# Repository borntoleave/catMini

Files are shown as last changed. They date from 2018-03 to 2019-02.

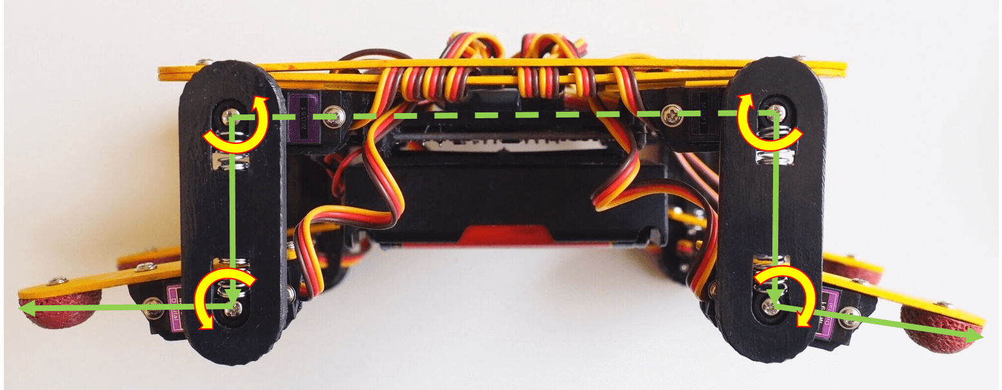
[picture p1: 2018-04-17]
Images/calibration.png

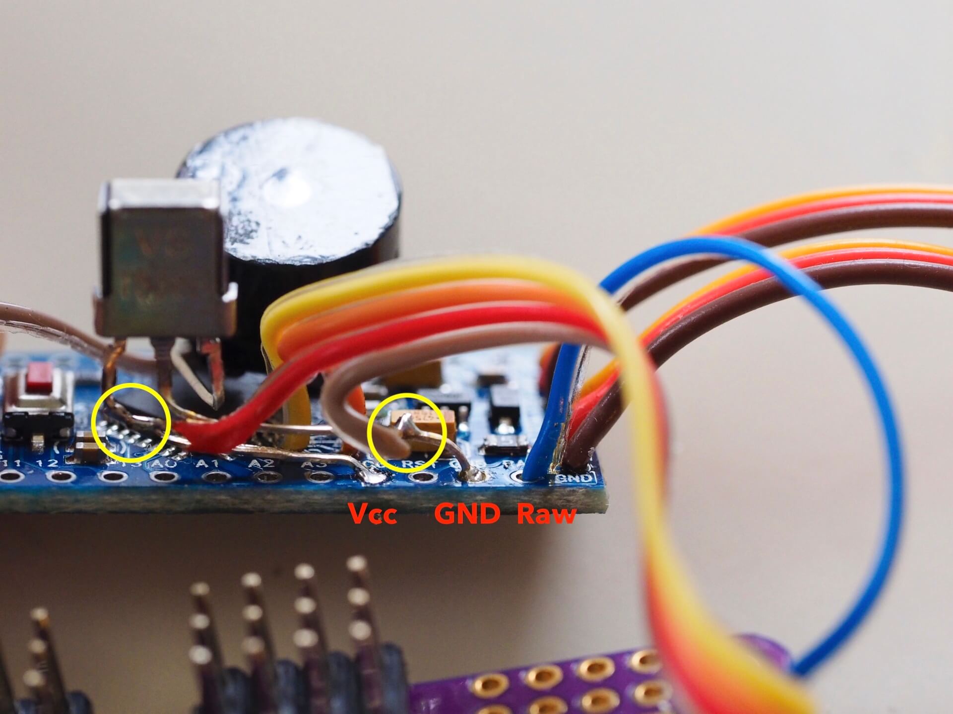
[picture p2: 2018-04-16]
Images/6.jpg

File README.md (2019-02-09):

# catMini
This is the course repository for catMini. Check out this demo video with my students racing them! https://youtu.be/T1OEnOONbIA

Structure
* Images/blockDiagram.png shows the circuit connection for catMini
* The test* folders with Arduino sketches are used for testing individual components' connections.
* writeConst folder contains the sketch to be uploaded to Arduino for storing calibration data
* catMini is the final sketch to be uploaded

This repo is obsolete since I've moved to my official repo for OpenCat: https://github.com/PetoiCamp/OpenCat
You can still find something interesting here.

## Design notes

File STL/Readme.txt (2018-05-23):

Recommanded Settings:
  material: ABS
  layer height: 0.1mm 
  infill: 100% 

Read the assmebling instructions in wiki thoroughly beforehand to understand how things are assembled. 

miniBody1 and miniBody2 shows the dimensions of the wooden frame. You can print them, but wooden ones are faster to make and has better strengh along the fiber direction. 

miniThigh holds the servo arm and allows it slide in the track. A spring pushes the servo arm in position. Check the assembling instructions for details.

miniToe is an old solution to increase friction. It should be printed with rubber-like soft material. 
I'm going to re-design a finger thimble like toe to replace it. 

Use M2 self-tapping screws to fix the frame and parts.

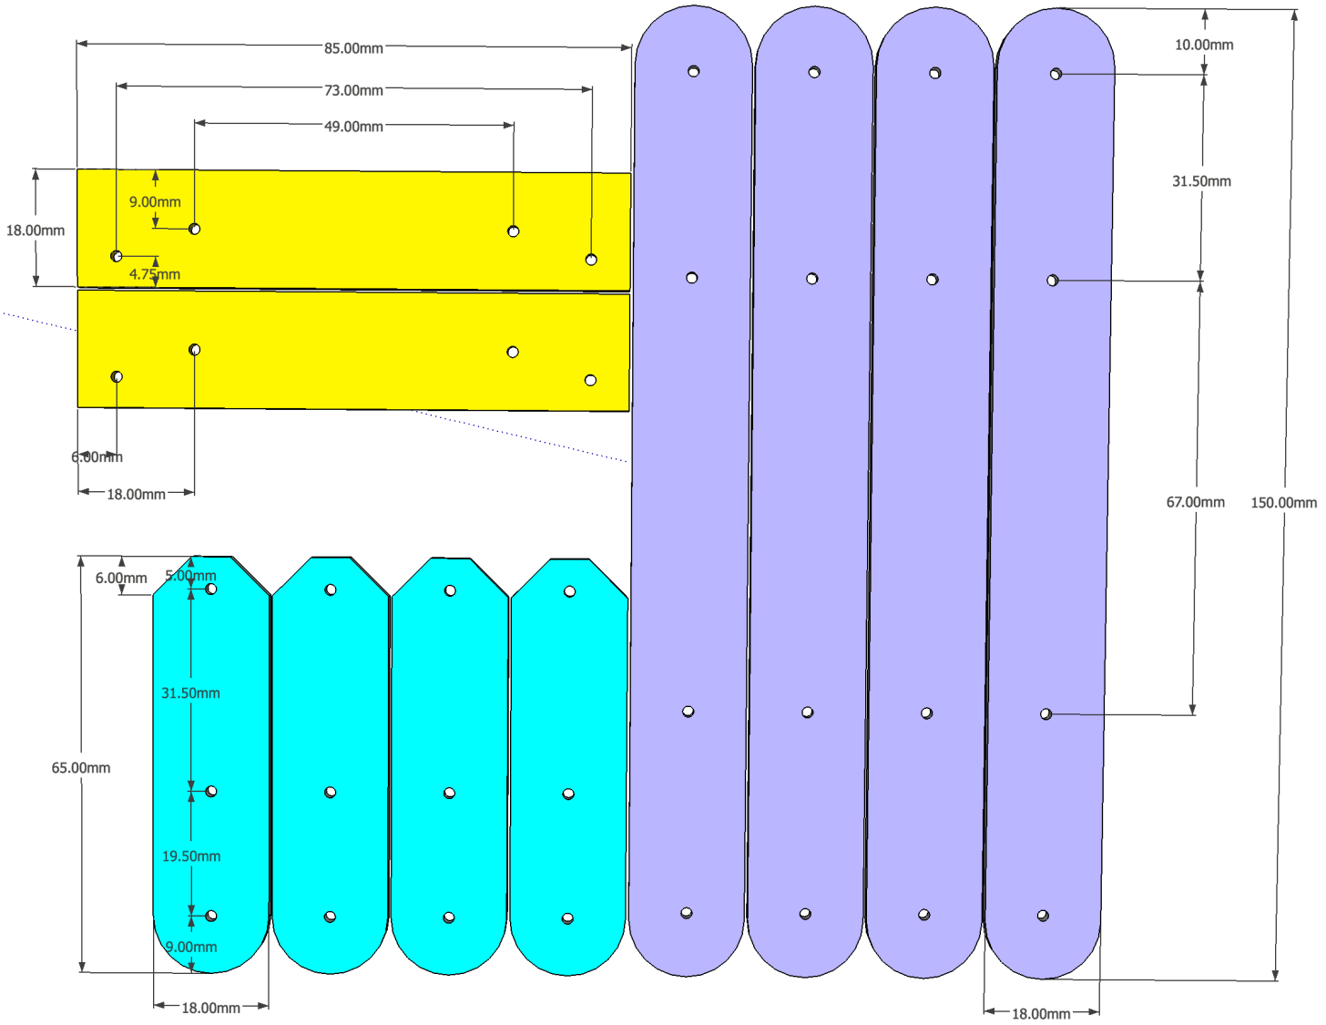
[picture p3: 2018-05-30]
Images/frameDim.png

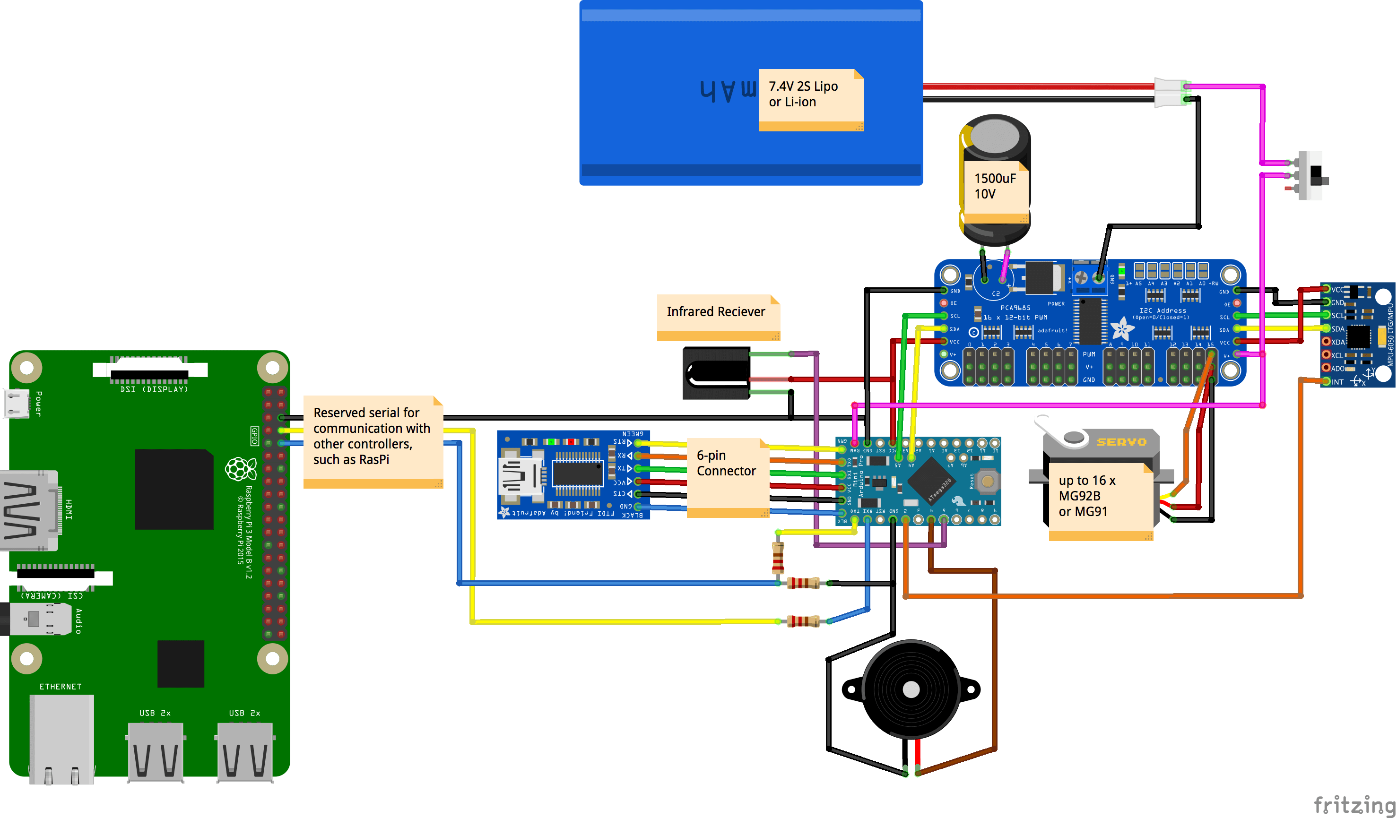
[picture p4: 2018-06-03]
Images/blockDiagram.png

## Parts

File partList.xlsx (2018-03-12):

Part List
 | Items | Quantity
Circuit | 18650/18500/14500 battery | 2
 | 2S battery holder | 1
 | slide switch | 1
 | MG91D/MG92B servos | 8
 | arduino pro mini 16Mhz 5V | 1
 | usb cable to mini usb | 1
 | FTDI | 1
 | MPU6050 | 1
 | PCA9685 servo driver | 1
 | IR remote kit | 1
 | 5V buzzer | 1
Frame | ABS filament | 1
 | spring | 8
 | Misc lab supply (wires, screws, box, etc)
 | 3D Printing and post processing (hrs) | 7

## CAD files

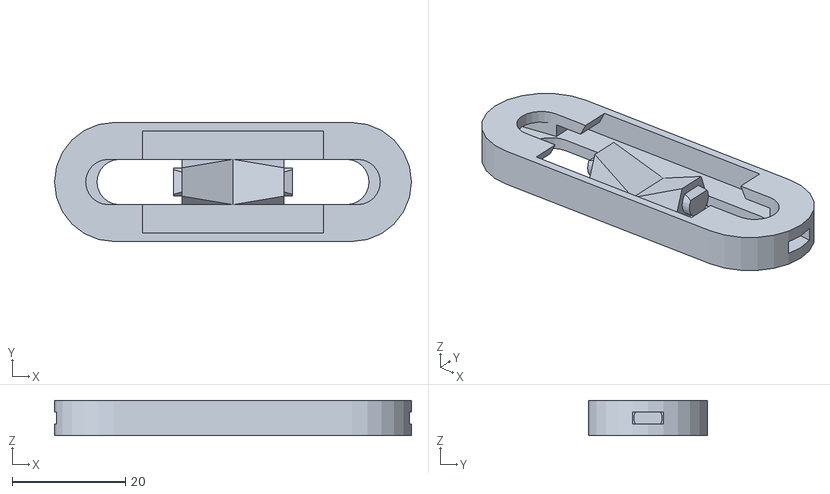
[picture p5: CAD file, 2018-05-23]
STL/1_miniThigh.stl
63.0 x 21.0 x 6.20

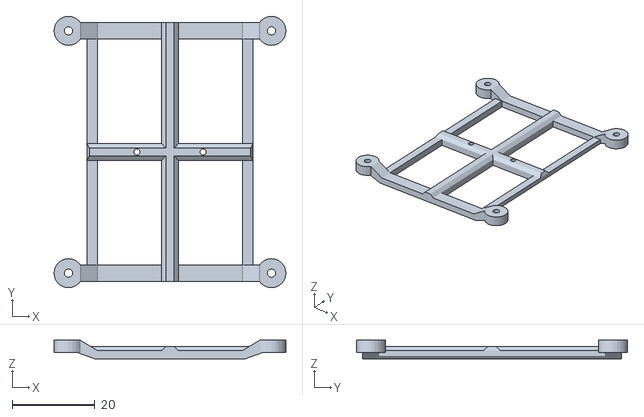
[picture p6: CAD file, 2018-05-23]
STL/mini_14500.stl
56.0 x 65.5 x 4.50

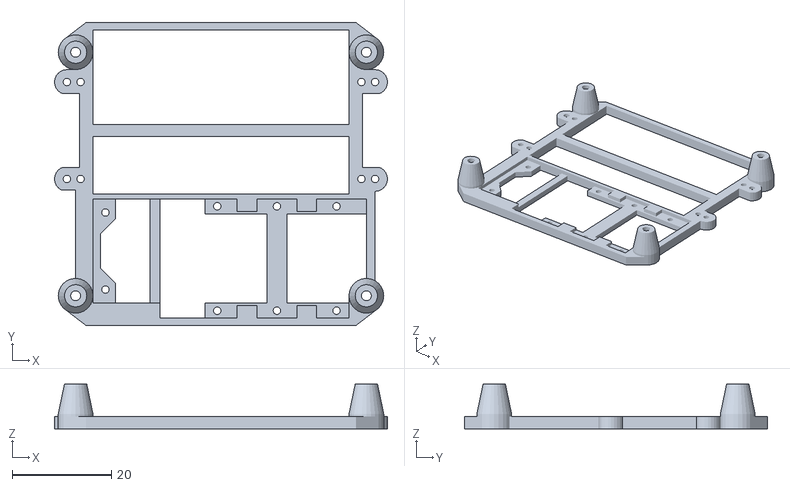
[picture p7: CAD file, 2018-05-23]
STL/miniCircuit.stl
67.0 x 61.0 x 9.00

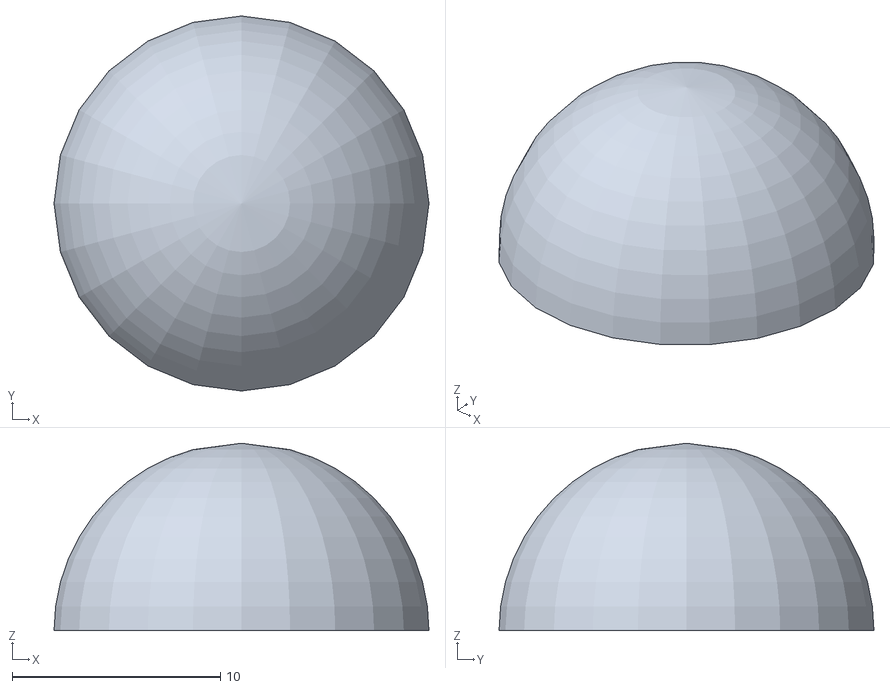
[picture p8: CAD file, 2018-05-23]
STL/1_miniToe_rubber.stl
18.0 x 18.0 x 9.00

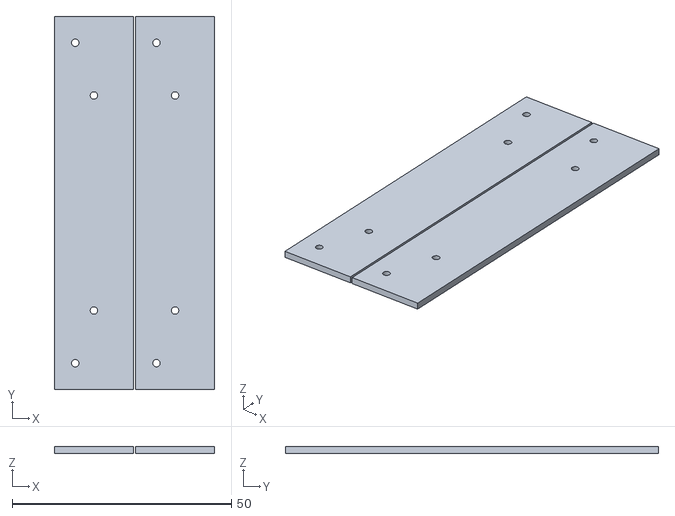
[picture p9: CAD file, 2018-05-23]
STL/all_miniBodyB.stl
36.5 x 85.0 x 1.50

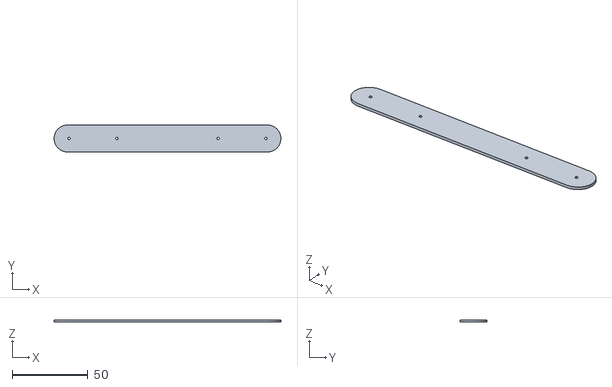
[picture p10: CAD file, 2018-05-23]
STL/1_miniBodyA.stl
150.0 x 18.0 x 1.50

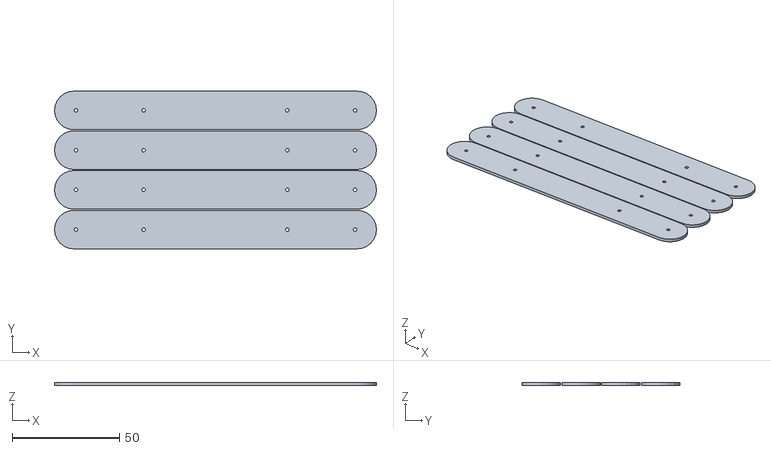
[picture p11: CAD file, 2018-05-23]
STL/all_miniBodyA.stl
150.0 x 73.5 x 1.50

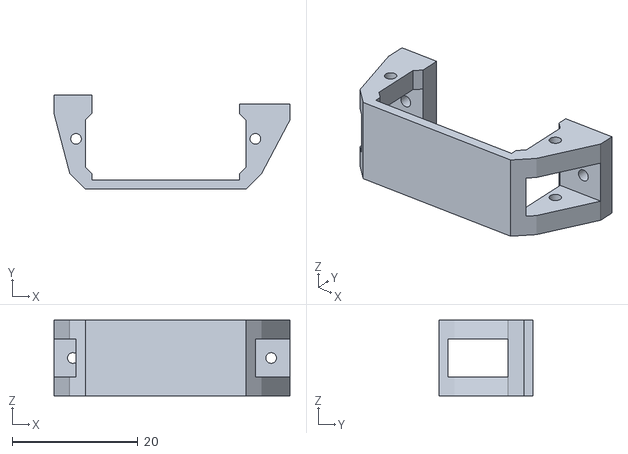
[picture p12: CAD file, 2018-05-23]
STL/1_miniServoHolder.stl
37.5 x 15.0 x 12.0

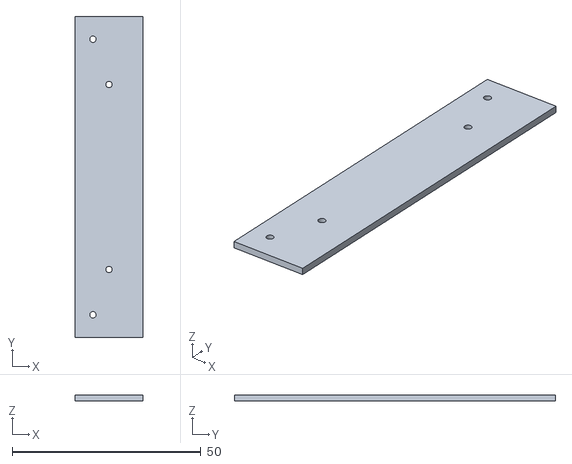
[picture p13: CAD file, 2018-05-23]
STL/1_miniBodyB.stl
18.0 x 85.0 x 1.50

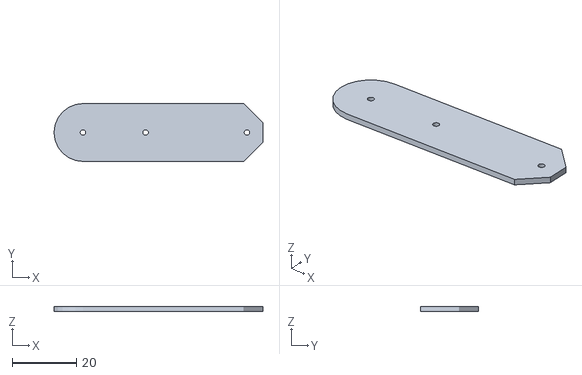
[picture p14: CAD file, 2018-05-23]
STL/1_miniShank.stl
65.0 x 18.0 x 1.50

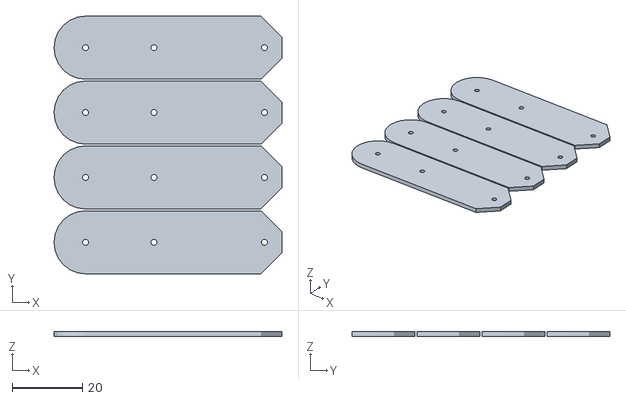
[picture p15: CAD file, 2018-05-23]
STL/all_miniShank.stl
65.0 x 73.5 x 1.50

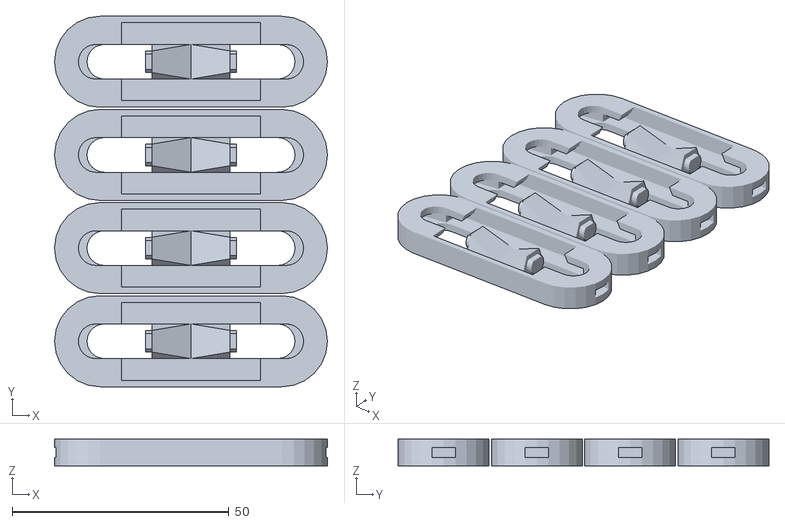
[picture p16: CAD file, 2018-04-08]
STL/all_miniThigh.stl
63.0 x 85.5 x 6.20

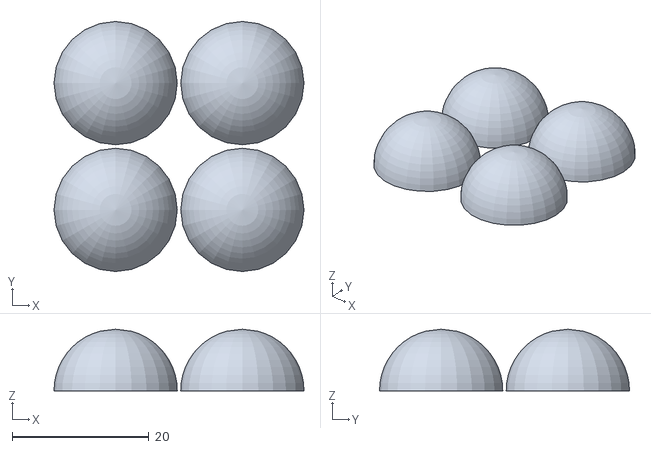
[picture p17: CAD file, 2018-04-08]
STL/all_miniToe_rubber.stl
36.5 x 36.5 x 9.00

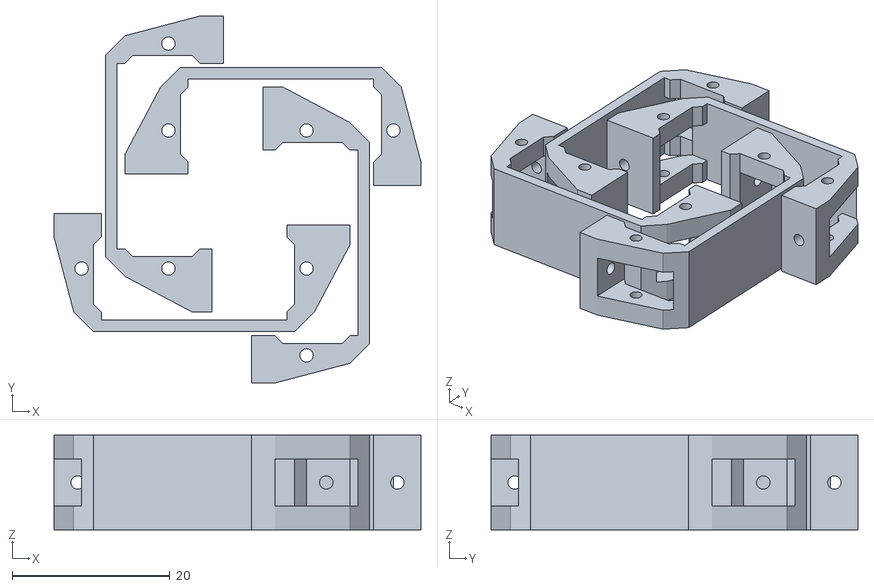
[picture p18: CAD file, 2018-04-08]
STL/all_miniServoHolder.stl
46.5 x 46.5 x 12.0

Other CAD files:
STL/mini_18650.stl

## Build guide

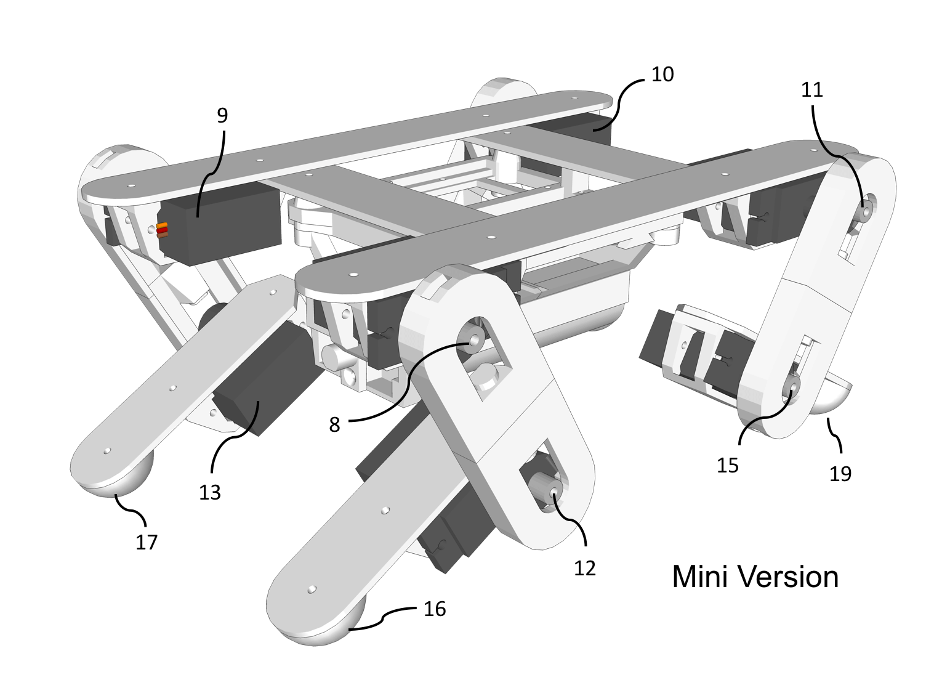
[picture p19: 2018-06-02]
Images/assembled.png

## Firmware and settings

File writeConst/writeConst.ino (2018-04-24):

/*
 *  Save calibration data and constants to EEPROM
 *  
 *  Copyright (c) 2018 Petoi LLC.  All right reserved.
 *  Written by Rongzhong Li
 *  
 *  This sketch also includes others' codes under MIT liscence. 
 *  See those liscences in corresponding sections.
 */

#define INIT true
#define LITE true
#include <EEPROM.h>
#define SPT(s) Serial.print(s)
#define SPTL(s) Serial.println(s)
#define SPTF(s) Serial.print(F(s))

#define MELODY 1023
#define PIN 0
#define CALIB 16
#define MIDSHIFT 32
#define ROTDIRECTION 48
#define RANGERATIO 64
#define MPUCALIB 80

#define DOF 16
#include <Wire.h>
#include <Adafruit_PWMServoDriver.h>

// called this way, it uses the default address 0x40
Adafruit_PWMServoDriver pwm = Adafruit_PWMServoDriver();
// you can also call it with a different address you want
//Adafruit_PWMServoDriver pwm = Adafruit_PWMServoDriver(0x41);

// Depending on your servo make, the pulse width min and max may vary, you
// want these to be as small/large as possible without hitting the hard stop
// for max range. You'll have to tweak them as necessary to match the servos you
// have!
#define SERVOMIN  150 // this is the 'minimum' pulse length count (out of 4096)
#define SERVOMAX  600 // this is the 'maximum' pulse length count (out of 4096)
#define BOUND 1/8
int range = SERVOMAX - SERVOMIN;
// our servo # counter

int8_t servoCalibs[DOF] = {};
char currentAng[DOF] = {};
int calibratedDuty0[DOF];
const char *gaits[] = {"vt", "rest", "calib", "balance",};
const char vt[] PROGMEM = { 30,
                            3, -3, -2,  2, 51, 45, 27, 22, -12,  3,  6, 22,
                            3, -2, -2,  2, 49, 45, 25, 22, -6,  3, 13, 22,
                            3, -2, -2,  1, 45, 45, 22, 22,  3,  3, 22, 22,
                            3, -1, -2,  1, 45, 45, 22, 22,  3,  3, 22, 22,
                            3, -1, -2,  1, 45, 45, 22, 22,  3,  3, 22, 22,
                            2,  1, -1,  1, 45, 46, 22, 22,  3,  1, 22, 20,
                            2,  1, -1, -1, 45, 49, 22, 25,  3, -6, 22, 13,
                            1,  2, -1, -1, 45, 51, 22, 27,  3, -12, 22,  6,
                            1,  2,  1, -1, 45, 54, 22, 29,  3, -19, 22,  1,
                            -1,  3,  1, -2, 45, 56, 22, 31,  3, -25, 22, -6,
                            -1,  3,  1, -2, 45, 59, 22, 33,  3, -33, 22, -12,
                            -2,  3,  1, -2, 45, 59, 22, 32,  3, -31, 22, -11,
                            -2,  3,  2, -2, 45, 56, 22, 31,  3, -25, 22, -6,
                            -3,  3,  2, -2, 45, 54, 22, 29,  3, -19, 22,  1,
                            -3,  3,  2, -2, 45, 51, 22, 27,  3, -12, 22,  6,
                            -3,  3,  2, -2, 45, 49, 22, 25,  3, -6, 22, 13,
                            -3,  3,  2, -2, 45, 45, 22, 22,  3,  3, 22, 22,
                            -2,  3,  2, -2, 45, 45, 22, 22,  3,  3, 22, 22,
                            -2,  3,  1, -2, 45, 45, 22, 22,  3,  3, 22, 22,
                            -1,  2,  1, -1, 45, 45, 22, 22,  3,  3, 22, 22,
                            -1,  2,  1, -1, 45, 45, 22, 22,  3,  3, 22, 22,
                            1,  1,  1, -1, 46, 45, 22, 22,  1,  3, 20, 22,
                            1,  1, -1,  1, 49, 45, 25, 22, -6,  3, 13, 22,
                            2, -1, -1,  1, 51, 45, 27, 22, -12,  3,  6, 22,
                            2, -1, -1,  1, 54, 45, 29, 22, -19,  3,  1, 22,
                            3, -2, -2,  1, 56, 45, 31, 22, -25,  3, -6, 22,
                            3, -2, -2,  2, 59, 45, 33, 22, -33,  3, -12, 22,
                            3, -3, -2,  2, 59, 45, 32, 22, -31,  3, -11, 22,
                            3, -3, -2,  2, 56, 45, 31, 22, -25,  3, -6, 22,
                            3, -3, -2,  2, 54, 45, 29, 22, -19,  3,  1, 22,
                            '\0'
                          };


const char rest[] PROGMEM = { 1,
                              1, 10,  1,  1, -3, -3,  3,  3, 60, 60, 60, 60, -30, -30, -30, -30, '\0'
                            };
const char calib[] PROGMEM = { 1,
                               1,  1,  1,  1,  1,  1,  1,  1,  1,  1,  1,  1,  1,  1,  1,  1, '\0'
                             };
const char balance[] PROGMEM = { 1,
                                 1, 20,  1,  1, -3, -3,  3,  3, 30, 30, 30, 30, 30, 30, 30, 30, '\0'
                               };
const char* const gaits_table[] PROGMEM = {vt, rest, calib, balance, };
char *dutyAng = new char [362];

void saveCalib(int8_t *var) {
  for (byte i = 0; i < DOF; i++) {
    EEPROM.update(CALIB + i, var[i]);
    calibratedDuty0[i] = SERVOMIN + range / 2 + float(middleShift(i) + var[i]) * range  * rotationDirection(i) / rangeRatio(i);
  }
}

void saveMPUcalib(int * var) {
  for (byte i = 0; i < 6; i++)
    EEPROM.update(MPUCALIB + i, var[i]);
}

void calibratedPWM(byte i, char dt) {
  currentAng[i] = dt;
  int duty = calibratedDuty0[i] + float(dt) * range  * rotationDirection(i) / rangeRatio(i);
  duty = min(SERVOMAX - range / 2 * BOUND, duty);
  duty = max(SERVOMIN + range / 2 * BOUND, duty);
  pwm.setPWM(pin(i), 0, duty);
}
void allCalibratedPWM(char * dutyAng) {
  for (byte i = 0; i < DOF; i++) {
    calibratedPWM(i, dutyAng[i]);
  }
}

void transform(char * current, char * target, byte offset = 0, float speedRatio = 1) {
  int *diff = new int[DOF - offset], maxDiff = 0;
  for (byte i = offset; i < DOF; i++) {
    diff[i - offset] =   current[i] - target[i - offset];
    maxDiff = max(maxDiff, abs( diff[i - offset]));
  }
  int steps = int(round(maxDiff / 3.0/*degreeStep*/ / speedRatio));
  for (byte s = 0; s < steps; s++)
    for (byte i = offset; i < DOF; i++) {
      int duty = (target[i] + (1 + cos(M_PI * s / steps)) / 2 * diff[i - offset]);
      calibratedPWM(i,  duty);
    }
  delete [] diff;
}

void shutServos() {
  delay(1000);
  for (byte i = 0; i < DOF; i++) {
    pwm.setPWM(i, 0, 4096);
  }
}

int8_t idxOfGait(const char * gait) {
  for (byte i = 0; i < sizeof(gaits) / sizeof(char*); i++)
    if (!strcmp(gaits[i], gait))
      return i;
  return -1;
}

int pgmCpy(char * dutyAng, const char * gait) {
  dutyAng--;
  strcpy_P(dutyAng, (char*)pgm_read_word(&(gaits_table[idxOfGait(gait)])));
  int period = dutyAng[0];
  dutyAng++;
  return period;
}

#include <EEPROM.h> //Needed to access the eeprom read write functions

byte pin(byte idx) {
  return (byte)EEPROM.read(PIN + idx);
}

int8_t middleShift(byte idx) {
  return (int8_t)EEPROM.read( MIDSHIFT + idx);
}
byte rangeRatio(byte idx) {
  return (byte)EEPROM.read(RANGERATIO + idx);
}
int8_t rotationDirection(byte idx) {
  return (int8_t)EEPROM.read(ROTDIRECTION + idx);
}
int8_t servoCalib(byte idx) {
  return (int8_t)EEPROM.read( CALIB + idx);
}

//This function will write a 2 byte integer to the eeprom at the specified address and address + 1
void EEPROMWriteInt(int p_address, int p_value)
{
  byte lowByte = ((p_value >> 0) & 0xFF);
  byte highByte = ((p_value >> 8) & 0xFF);

  EEPROM.update(p_address, lowByte);
  EEPROM.update(p_address + 1, highByte);
}

//This function will read a 2 byte integer from the eeprom at the specified address and address + 1
int EEPROMReadInt(int p_address)
{
  byte lowByte = EEPROM.read(p_address);
  byte highByte = EEPROM.read(p_address + 1);

  return ((lowByte << 0) & 0xFF) + ((highByte << 8) & 0xFF00);
}

void writeConst(bool lite = true) {
  // tone: pause,1,  2,  3,  4,  5,  6,  7,  1,  2, 3,
  // code: 0,    1,  3,  5,  6,  8,  10, 12, 13, 15, 17
  byte melody[] = {8, 13, 10, 13, 8,  0,  5,  8,  3,  5, 8,
                   8, 8,  32, 32, 8, 32, 32, 32, 32, 32, 8,
                  };
  EEPROM.update(MELODY, sizeof(melody));
  for (byte i = 0; i < sizeof(melody); i++)
    EEPROM.update(MELODY - 1 - i, melody[i]);

  int8_t calibs[] = {0,  0,  0,  0,  0,  0,  0,  0,  0,  0,  0,  0,  0,  0,  0,  0};

  int8_t middleShifts[] = {0, 45, 0, 0,
                           -45, -45, -45, -45,
                           0, 0, 0, 0,
                           0, 0, 0, 0
                          };
  int8_t rotationDirections[] = {1, -1, 1, 1,
                                 1, -1, 1, -1,
                                 1, -1, 1, -1,
                                 -1, 1, -1, 1
                                };
  byte mg90s = 180 , mg92b =  180;
  byte rangeRatios[] =  {mg92b, mg90s, mg92b, mg92b,
                         mg92b, mg92b, mg92b, mg92b,
                         mg92b, mg92b, mg92b, mg92b,
                         mg92b, mg92b, mg92b, mg92b
                        };

  for (byte i = 0; i < DOF; i++) {
    if (lite) {
      byte pins[] = {0, 0, 0, 0, 0, 0, 0, 0, 5, 4, 10, 11, 7, 6,8, 9};
      //byte pins[] = { 0, 1, 0, 0,  0, 0,  0, 0, 3, 2,  6, 7,  5, 4,  8, 9};
      EEPROM.update(PIN + i, pins[i]);
    }
    else {
      byte pins[] = { 1, 0, 15, 14,  3, 2,  8, 9, 5, 4,  10, 11,  7, 6,  12, 13};
      EEPROM.update(PIN + i, pins[i]);
    }
    if (INIT)
      EEPROM.update(CALIB + i, calibs[i]);
    EEPROM.update(MIDSHIFT + i, middleShifts[i]);
    EEPROM.update(ROTDIRECTION + i, rotationDirections[i]);
    EEPROM.update(RANGERATIO + i, rangeRatios[i]);
    SPT(servoCalib(i));
    SPT(',');
  }
  SPT('\n');
}

#define BUZZER 4
#define MELODY 1023
void beep(byte note, float duration = 10, int pause = 0, byte repeat = 1 ) {
  if (note == 0) {
    analogWrite(BUZZER, 0);
    delay(duration);
    return;
  }
  int freq = 220 * pow(1.059463, note);
  float period = 1000000.0 / freq / 2.0;
  for (byte r = 0; r < repeat; r++) {
    for (float t = 0; t < duration * 1000; t += period * 2) {
      analogWrite(BUZZER, 150);      // Almost any value can be used except 0 and 255
      // experiment to get the best tone
      delayMicroseconds(period);          // wait for a delayms ms
      analogWrite(BUZZER, 0);       // 0 turns it off
      delayMicroseconds(period);          // wait for a delayms ms
    }
    delay(pause);
  }
}

// http://wired.chillibasket.com/2015/01/calibrating-mpu6050/

// Arduino sketch that returns calibration offsets for MPU6050
//   Version 1.1  (31th January 2014)
// Done by Luis Ródenas <luisrodenaslorda@gmail.com>
// Based on the I2Cdev library and previous work by Jeff Rowberg <jeff@rowberg.net>
// Updates (of the library) should (hopefully) always be available at https://github.com/jrowberg/i2cdevlib

// These offsets were meant to calibrate MPU6050's internal DMP, but can be also useful for reading sensors.
// The effect of temperature has not been taken into account so I can't promise that it will work if you
// calibrate indoors and then use it outdoors. Best is to calibrate and use at the same room temperature.

/* ==========  LICENSE  ==================================
  I2Cdev device library code is placed under the MIT license
  Copyright (c) 2011 Jeff Rowberg

  Permission is hereby granted, free of charge, to any person obtaining a copy
  of this software and associated documentation files (the "Software"), to deal
  in the Software without restriction, including without limitation the rights
  to use, copy, modify, merge, publish, distribute, sublicense, and/or sell
  copies of the Software, and to permit persons to whom the Software is
  furnished to do so, subject to the following conditions:

  The above copyright notice and this permission notice shall be included in
  all copies or substantial portions of the Software.

  THE SOFTWARE IS PROVIDED "AS IS", WITHOUT WARRANTY OF ANY KIND, EXPRESS OR
  IMPLIED, INCLUDING BUT NOT LIMITED TO THE WARRANTIES OF MERCHANTABILITY,
  FITNESS FOR A PARTICULAR PURPOSE AND NONINFRINGEMENT. IN NO EVENT SHALL THE
  AUTHORS OR COPYRIGHT HOLDERS BE LIABLE FOR ANY CLAIM, DAMAGES OR OTHER
  LIABILITY, WHETHER IN AN ACTION OF CONTRACT, TORT OR OTHERWISE, ARISING FROM,
  OUT OF OR IN CONNECTION WITH THE SOFTWARE OR THE USE OR OTHER DEALINGS IN
  THE SOFTWARE.
  =========================================================
*/

// I2Cdev and MPU6050 must be installed as libraries
#include "I2Cdev.h"
#include "MPU6050.h"
#include "Wire.h"

///////////////////////////////////   CONFIGURATION   /////////////////////////////
//Change this 3 variables if you want to fine tune the skecth to your needs.
int discard = 100;
int buffersize = 1000;   //Amount of readings used to average, make it higher to get more precision but sketch will be slower  (default:1000)
int acel_deadzone = 8;   //Acelerometer error allowed, make it lower to get more precision, but sketch may not converge  (default:8)
int giro_deadzone = 1;   //Giro error allowed, make it lower to get more precision, but sketch may not converge  (default:1)

// default I2C address is 0x68
// specific I2C addresses may be passed as a parameter here
// AD0 low = 0x68 (default for InvenSense evaluation board)
// AD0 high = 0x69
//MPU6050 mpu;
MPU6050 mpu(0x68); // <-- use for AD0 high

int16_t ax, ay, az, gx, gy, gz;

int mean_ax, mean_ay, mean_az, mean_gx, mean_gy, mean_gz, state = 0;
int ax_offset, ay_offset, az_offset, gx_offset, gy_offset, gz_offset;

int t = 0;
int tPeriod = 1;
byte offset;
char token;
#define CMD_LEN 10
char lastCmd[CMD_LEN] = {};
bool printMPU = false;
int mpuOffset[6];
void setup() {
  // join I2C bus (I2Cdev library doesn't do this automatically)
#if I2CDEV_IMPLEMENTATION == I2CDEV_ARDUINO_WIRE
  Wire.begin();
  TWBR = 24; // 400kHz I2C clock (200kHz if CPU is 8MHz)
#elif I2CDEV_IMPLEMENTATION == I2CDEV_BUILTIN_FASTWIRE
  Fastwire::setup(400, true);
#endif

  Serial.begin(57600);
  Serial.setTimeout(5);
  while (!Serial);

  for (byte i = 0; i < 6; i++)
    SPTL(EEPROMReadInt(MPUCALIB + i * 2));
  // initialize device
  mpu.initialize();

  // wait for ready
  while (Serial.available() && Serial.read()); // empty buffer
  /*while (!Serial.available()){
    Serial.println(F("Send any character to start sketch.\n"));
    delay(1500);
    }
    while (Serial.available() && Serial.read()); // empty buffer again
  */
  SPT(F("* RoPet Writing Constants to EEPROM *\n"));
  writeConst(LITE); // only run for the first time when writing to the board.

  // servo
  { pwm.begin();
    pwm.setPWMFreq(60);  // Analog servos run at ~60 Hz updates
    delay(200);

    strcpy(lastCmd, "rest");
    pgmCpy(dutyAng, "rest");
    for (byte i = 0; i < DOF; i++) {
      servoCalibs[i] = servoCalib(i);
      calibratedDuty0[i] =  SERVOMIN + range / 2 + float(middleShift(i) + servoCalibs[i]) * range   * rotationDirection(i) / rangeRatio(i);
      calibratedPWM(i, dutyAng[i]);
    }
    shutServos();
    token = 'd';
  }
  beep(30);

  // start message
  Serial.println("\nMPU6050 Calibration Sketch");
  delay(2000);
  Serial.println("\nYour MPU6050 should be placed in horizontal position, with package letters facing up. \nDon't touch it until you see a finish message.\n");
  delay(3000);
  // verify connection
  Serial.println(mpu.testConnection() ? "MPU6050 connection successful" : "MPU6050 connection failed");
  delay(1000);
  // reset offsets
  mpu.setXAccelOffset(0);
  mpu.setYAccelOffset(0);
  mpu.setZAccelOffset(0);
  mpu.setXGyroOffset(0);
  mpu.setYGyroOffset(0);
  mpu.setZGyroOffset(0);
}

void loop() {
  if (state == 0) {
    Serial.println("\nReading sensors for first time...");
    meansensors();
    state++;
    delay(1000);
  }

  if (state == 1) {
    Serial.println("\nCalculating offsets...");
    calibration();
    state++;
    delay(1000);
  }

  if (state == 2) {
    meansensors();
    Serial.println("\nFINISHED!");
    Serial.print("\nSensor readings with offsets:\t");
    Serial.print(mean_ax);
    Serial.print("\t");
    Serial.print(mean_ay);
    Serial.print("\t");
    Serial.print(mean_az);
    Serial.print("\t");
    Serial.print(mean_gx);
    Serial.print("\t");
    Serial.print(mean_gy);
    Serial.print("\t");
    Serial.println(mean_gz);
    Serial.print("Your offsets:\t");
    Serial.print(ax_offset);
    Serial.print("\t");
    Serial.print(ay_offset);
    Serial.print("\t");
    Serial.print(az_offset);
    Serial.print("\t");
    Serial.print(gx_offset);
    Serial.print("\t");
    Serial.print(gy_offset);
    Serial.print("\t");
    Serial.println(gz_offset);
    Serial.println("\nData is printed as: acelX acelY acelZ giroX giroY giroZ");
    Serial.println("Check that your sensor readings are close to 0 0 16384 0 0 0");
    Serial.println("If calibration was succesful write down your offsets so you can set them in your projects using something similar to mpu.setXAccelOffset(youroffset)");

    mpuOffset[0] = ax_offset;
    mpuOffset[1] = ay_offset;
    mpuOffset[2] = az_offset;
    mpuOffset[3] = gx_offset;
    mpuOffset[4] = gy_offset;
    mpuOffset[5] = gz_offset;

    for (byte i = 0; i < 6; i++)
      EEPROMWriteInt(MPUCALIB + i * 2, mpuOffset[i]);

    mpu.setXAccelOffset(ax_offset);
    mpu.setYAccelOffset(ay_offset);
    mpu.setZAccelOffset(az_offset);
    mpu.setXGyroOffset(gx_offset);
    mpu.setYGyroOffset(gy_offset);
    mpu.setZGyroOffset(gz_offset);
    //while (1);
    state = 3;
  }

  char cmd[CMD_LEN] = {};
  byte newCmd = 0;
  if (t == 0 && Serial.available() > 0) {
    token = Serial.read();
    newCmd = 3;
  }
  if (newCmd) {
    beep(newCmd * 10);
    // this block handles argumentless tokens

    if (token == 'm')
      printMPU = !printMPU;
    if (token == 'h')
      SPTF("** Help Information **");// print the help document

    else if (token == 'd' ) {
      pgmCpy(dutyAng, "rest");
      transform(currentAng, dutyAng);
      SPTF("shut down servos");
      shutServos();
    }
    else if (token == 's') {
      SPT(F("save calibration"));
      saveCalib(servoCalibs);
    }
    else if (token == 'a') {
      SPT(F("abandon calibration"));
      for (byte i = 0; i < DOF; i++) {
        servoCalibs[i] = servoCalib( i);
      }
    }
    // this block handles array like arguments
    else if (token == 'c' || token == 't') {
      int target[2] = {};
      String inBuffer = Serial.readStringUntil('\n');
      strcpy(cmd, inBuffer.c_str());
      char *pch;
      pch = strtok (cmd, " ,");
      for (int c = 0; pch != NULL; c++)
      {
        target[c] = atoi(pch);
        pch = strtok (NULL, " ,");
      }

      if (token == 'c') {
        //SPTF("calibrating [ targetIdx, angle ]: ");
        if (strcmp(lastCmd, "c")) { //first time entering the calibration function
          pgmCpy(dutyAng, "calib");
          transform(currentAng, dutyAng);
          shutServos();
        }
        SPT('\n');
        for (byte i = 0; i < DOF; i++) {
          SPT(i);
          SPT(",\t");
        }
        SPT('\n');
        for (byte i = 0; i < DOF; i++) {
          SPT(servoCalibs[i]);
          SPT(",\t");
        }
        SPT('\n');
        yield();
        servoCalibs[target[0]] = target[1];
      }
      else if (token == 't') {
        //SPTF("moving [ targetIdx, angle ]: ");
        dutyAng[target[0]] = target[1];
      }

      SPT(target[0]);
      SPT(",\t");
      SPT(target[1]);

      int duty = SERVOMIN + range / 2 + float(middleShift(target[0])  + servoCalibs[target[0]] + dutyAng[target[0]]) * range * rotationDirection(target[0]) / rangeRatio(target[0]);
      pwm.setPWM(pin(target[0]), 0,  duty);
      shutServos();
    }

    else if (Serial.available() > 0) {
      String inBuffer = Serial.readStringUntil('\n');
      strcpy(cmd, inBuffer.c_str());
    }
    while (Serial.available() && Serial.read()); //flush the remaining serial buffer in case the commands are parsed incorrectly

    if (strcmp(cmd, "") && strcmp(lastCmd, cmd) ) {
      if (token == 'p' || token == 'g') { //validating key
        if (idxOfGait(cmd) >= 0) {
          tPeriod =  pgmCpy(dutyAng, cmd);
          t = 0;
          if (strcmp(cmd, "balance") )
            strcpy(lastCmd, cmd);
          offset = (tPeriod == 1) ? 0 : 4;
          transform(currentAng, dutyAng, offset, 0.5);
        }
        else
          SPT(F("wrong key!\n"));
      }
      else {
        lastCmd[0] = token;
        memset(lastCmd + 1, '\0', CMD_LEN - 1);
      }
    }
  }

  //motion block
  {
    if (printMPU) {
      mpu.getMotion6(&ax, &ay, &az, &gx, &gy, &gz);
      SPTF("ax\tay\taz\tgx\tgy\tgz: ");
      SPT(ax);
      SPT('\t');
      SPT(ay);
      SPT('\t');
      SPT(az);
      SPT('\t');
      SPT(gx);
      SPT('\t');
      SPT(gy);
      SPT('\t');
      SPT(gz);
      SPT('\n');
    }
    if (token == 'p' || token == 'g') {
      for (int i = offset; i < DOF; i++) {
        int dutyIdx =  t * 12 - offset + i;
        calibratedPWM(pin(i), dutyAng[dutyIdx]);

      }
      t = (t + 1) % tPeriod;

      delay(30);
    }
  }
}

void meansensors() {
  long i = 0, buff_ax = 0, buff_ay = 0, buff_az = 0, buff_gx = 0, buff_gy = 0, buff_gz = 0;

  while (i < (buffersize + discard + 1)) {
    // read raw accel/gyro measurements from device
    mpu.getMotion6(&ax, &ay, &az, &gx, &gy, &gz);

    if (i > discard && i <= (buffersize + discard)) { //First 100 measures are discarded
      buff_ax = buff_ax + ax;
      buff_ay = buff_ay + ay;
      buff_az = buff_az + az;
      buff_gx = buff_gx + gx;
      buff_gy = buff_gy + gy;
      buff_gz = buff_gz + gz;
    }
    if (i == (buffersize + discard)) {
      mean_ax = buff_ax / buffersize;
      mean_ay = buff_ay / buffersize;
      mean_az = buff_az / buffersize;
      mean_gx = buff_gx / buffersize;
      mean_gy = buff_gy / buffersize;
      mean_gz = buff_gz / buffersize;
    }
    i++;
    delay(2); //Needed so we don't get repeated measures
  }
}
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

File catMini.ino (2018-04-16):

#define SPT(s) Serial.print(s)
#define SPTL(s) Serial.println(s)
#define SPTF(s) Serial.print(F(s))
#define SPLF(s) Serial.println(F(s))

#include "I2Cdev.h"
#include "MPU6050_6Axis_MotionApps20.h"

MPU6050 mpu;
//#define OUTPUT_READABLE_YAWPITCHROLL

// MPU control/status vars
bool dmpReady = false;  // set true if DMP init was successful
uint8_t mpuIntStatus;   // holds actual interrupt status byte from MPU
uint8_t devStatus;      // return status after each device operation (0 = success, !0 = error)
uint16_t packetSize;    // expected DMP packet size (default is 42 bytes)
uint16_t fifoCount;     // count of all bytes currently in FIFO
uint8_t fifoBuffer[64]; // FIFO storage buffer

// orientation/motion vars
Quaternion q;           // [w, x, y, z]         quaternion container
VectorFloat gravity;    // [x, y, z]            gravity vector
float ypr[3], yprLag[2][3];         // [yaw, pitch, roll]   yaw/pitch/roll container and gravity vector
bool overFlow = false;

// ================================================================
// ===               INTERRUPT DETECTION ROUTINE                ===
// ================================================================

volatile bool mpuInterrupt = false;     // indicates whether MPU interrupt pin has gone high
void dmpDataReady() {
  mpuInterrupt = true;
}

#include <EEPROM.h>
//#include <avr/eeprom.h>
#define BUZZER 4
#define MELODY 1023
void beep(byte note, float duration = 10, int pause = 0, byte repeat = 1 ) {
  if (note == 0) {
    analogWrite(BUZZER, 0);
    delay(duration);
    return;
  }
  int freq = 220 * pow(1.059463, note);
  float period = 1000000.0 / freq / 2.0;
  for (byte r = 0; r < repeat; r++) {
    for (float t = 0; t < duration * 1000; t += period * 2) {
      analogWrite(BUZZER, 150);      // Almost any value can be used except 0 and 255
      // experiment to get the best tone
      delayMicroseconds(period);          // wait for a delayms ms
      analogWrite(BUZZER, 0);       // 0 turns it off
      delayMicroseconds(period);          // wait for a delayms ms
    }
    delay(pause);
  }
}
void playMelody(int start) {
  byte len = (byte)EEPROM.read(start) / 2;
  for (int i = 0; i < len; i++)
    beep(EEPROM.read(start - 1 - i), 1000 / EEPROM.read(start - 1 - len - i), 100);
}

// https://brainy-bits.com/blogs/tutorials/ir-remote-arduino
#include "IRremote.h"
int receiver = 5; // Signal Pin of IR receiver to Arduino Digital Pin 5
/*-----( Declare objects )-----*/
IRrecv irrecv(receiver);     // create instance of 'irrecv'
decode_results results;      // create instance of 'decode_results'
String translateIR() // takes action based on IR code received
// describing Remote IR codes. 
{                                     
  switch (results.value) {
                 //abbreviation of gaits      key on IR remote                gait/posture names
    case 0xFF629D: return (F("vt"));        //Serial.println(" FORWARD");   //stepping on spot, "mark time"
    case 0xFF22DD: return (F("sit"));       //Serial.println(" LEFT");      //sit
    case 0xFF02FD: return (F("bd"));        //Serial.println(" -OK-");      //bound
    case 0xFFC23D: return (F("balance"));   //Serial.println(" RIGHT");     //standing
    case 0xFFA857: return (F("d"));         //Serial.println(" REVERSE");   //shut down servos
    case 0xFF6897: return (F("trL"));       //Serial.println(" 1");         //trot left
    case 0xFF9867: return (F("tr"));        //Serial.println(" 2");         //trot 
    case 0xFFB04F: return (F("trR"));       //Serial.println(" 3");         //trot right
    case 0xFF30CF: return (F("wkL"));       //Serial.println(" 4");         //walk left
    case 0xFF18E7: return (F("wk"));        //Serial.println(" 5");         //walk 
    case 0xFF7A85: return (F("wkR"));       //Serial.println(" 6");         //walk right
    case 0xFF10EF: return (F("crL"));       //Serial.println(" 7");         //crawl left
    case 0xFF38C7: return (F("cr"));        //Serial.println(" 8");         //crawl
    case 0xFF5AA5: return (F("crR"));       //Serial.println(" 9");         //crawl right
    case 0xFF42BD: return (F("bkL"));       //Serial.println(" *");         //back left
    case 0xFF4AB5: return (F("bk"));        //Serial.println(" 0");         //back
    case 0xFF52AD: return (F("bkR"));       //Serial.println(" #");         //back right
    case 0xFFFFFFFF: return (""); //Serial.println(" REPEAT");

    default:
      return ("");                      //Serial.println("null");
  }// End Case
  //delay(100); // Do not get immediate repeat //no need because the main loop is slow
  
  // The control could be organized in another way, such as:
  // forward/backward to change the gaits corresponding to different speeds. 
  // left/right key for turning left and right
  // number keys for different postures or behaviors
}

#define DOF 16
const byte wakePin = 6;
#include <Wire.h>
#include <Adafruit_PWMServoDriver.h>

// called this way, it uses the default address 0x40
Adafruit_PWMServoDriver pwm = Adafruit_PWMServoDriver();
// you can also call it with a different address you want
//Adafruit_PWMServoDriver pwm = Adafruit_PWMServoDriver(0x41);

// Depending on your servo make, the pulse width min and max may vary, you
// want these to be as small/large as possible without hitting the hard stop
// for max range. You'll have to tweak them as necessary to match the servos you
// have!
#define SERVOMIN  150 // this is the 'minimum' pulse length count (out of 4096)
#define SERVOMAX  600 // this is the 'maximum' pulse length count (out of 4096)
#define BOUND 1/8
#define RANGE (SERVOMAX - SERVOMIN)
// our servo # counter

int8_t servoCalibs[DOF] = {};
char currentAng[DOF] = {};
#define FLAT 5
#define panF 1 / 2.0
#define tF 1.0
#define sXF 2
#define sYF 1/4.0
#define uF 0.8
#define dF -0.8
float coeff[16][2] = {
  { -panF, 0}, {0, -tF}, {0, 0}, {0, 0},
  {sXF, -sYF}, { -sXF, -sYF}, { -sXF, sYF}, {sXF, sYF},
  { uF, 1}, { -uF, 1}, { -uF , -1 }, { uF , -1 },
  { dF, dF}, { -dF, dF}, { -dF, -dF}, { dF, -dF}
};

int calibratedDuty0[DOF];

//movements and postures
#include "modes.h"


#define PIN 0
#define CALIB 16
#define MIDSHIFT 32
#define ROTDIRECTION 48
#define RANGERATIO 64
#define MPUCALIB 80


//This function will write a 2 byte integer to the eeprom at the specified address and address + 1
void EEPROMWriteInt(int p_address, int p_value)
{
  byte lowByte = ((p_value >> 0) & 0xFF);
  byte highByte = ((p_value >> 8) & 0xFF);
  EEPROM.update(p_address, lowByte);
  EEPROM.update(p_address + 1, highByte);
}

//This function will read a 2 byte integer from the eeprom at the specified address and address + 1
int EEPROMReadInt(int p_address)
{
  byte lowByte = EEPROM.read(p_address);
  byte highByte = EEPROM.read(p_address + 1);
  return ((lowByte << 0) & 0xFF) + ((highByte << 8) & 0xFF00);
}

byte pin(byte idx) {
  return (byte)EEPROM.read(PIN + idx);
}

int8_t middleShift(byte idx) {
  return (int8_t)EEPROM.read( MIDSHIFT + idx);
}
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

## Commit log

2018-03-12 add partList
    [partList.xlsx]
2018-03-12 add circuit block diagram
2018-03-14 changed pin number in buzzer
2018-04-08 added STL and images
    [miniArm.stl, miniBattLink.stl, miniFrame.stl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]
2018-04-17 add calibration
2018-04-17 add servo arm
2018-04-24 add beep to calibration
2018-05-22 Added STL file with only one servo mount
    [singleMiniArm.stl]
2018-05-23 added single models for parts and a readme.txt
    [1_miniBodyA.stl, 1_miniBodyB.stl, 1_miniServoHolder.stl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]
2018-05-23 add bom
    [miniBOM.csv]
2018-05-30 added frame dimensions and updated installation wiki
2018-05-30 modify frameDim.png
2018-05-30 corrected typo in BOM
    [miniBOM.csv]
2018-06-02 added diagram for servo index. updated wiki
2018-06-03 added the missing gnd conncection between arduino and battery in block diagram
